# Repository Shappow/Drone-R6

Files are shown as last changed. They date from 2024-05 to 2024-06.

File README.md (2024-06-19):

# BravaBot - General README
#### ⚠️ This project is a work in progress, not all features works and there are bugs ⚠️
The BravaBot is a project meant to make a remote controlled ground vehicule capable of shooting projectiles with a barrel. <br>
In this repository, you will have 4 major folders which describes every important part of the robot. They all have a README into it and that you must follow for to build the vehicule correctly. 
- Electrical Schematics and components you need
- 3D files 
- Android application made on Unity to pilot the vehicule
- Raspberry Pi files to setup and make the vehicule work <br>
The building instruction are into the "datasheet.pdf" file.

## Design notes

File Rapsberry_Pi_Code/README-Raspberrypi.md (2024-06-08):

# Rapsberry-Pi configuration
#### ⚠️Before making any of the following instructions, be sure to setup all of the electronics. You also need a SD card that has at least 16GB of space⚠️

Welcome to the configuration of the raspberry pi. This file will be seperated between to 3 major parts : 
1. Raspberry Pi Setup
2. Camera, Network and video-streaming
3. Motors and canon configuration

Be sure to make to follow in order the steps.

## 1. Raspberry Pi setup 
For this step you will need : 
- A RaspberryPi 3b+ 
- A microSD card which has at least 16GB of storage 
- A SD card/micro SD card reader for you computer/laptop if they  do not have one
- A monitor to connect to the raspberry pi via its HDMI port
- A mouse and keyboard to connect to the USB ports of the raspberry pi

#### ⚠️You will flash a new OS on your MicroSD card. Everything will be erased on it. Be sure to backup everything before making any further step. ⚠️

You can follow this tutorial to setup your raspberry pi 
https://www.youtube.com/watch?v=g2e9RTcXKwg <br>
However you must be aware of the differences :
- The device must be a raspberry pi 3B+
- You need to get the lastest OS version
- You only need to setup the Wifi in "edit settings" you can adapt your country if you want too

After setting up the raspberry pi, open a terminal and install git if not already done (you have to be connected to you wifi) : 
``` bash 
sudo apt-get update
sudo apt-get install -y git
```
And clone in a chosen folder this repository. 
``` bash
git clone https://github.com/Shappow/Drone-R6.git
```
Switch to the Raspberry Pi Branch to save space on your SD card
``` bash
git checkout Raspberry-Pi
```
## 2. Setting up the Network, Camera and Start the video-streaming
### Setting up the camera
For this you will need the **Raspberry-Pi Camera V2**. You can buy it [here](https://www.amazon.fr/Raspberry-Pi-1080p-Module-Caméra/dp/B01ER2SKFS/ref=asc_df_B01ER2SKFS/?tag=googshopfr-21&linkCode=df0&hvadid=194988968614&hvpos=&hvnetw=g&hvrand=10344806919070677782&hvpone=&hvptwo=&hvqmt=&hvdev=c&hvdvcmdl=&hvlocint=&hvlocphy=9055302&hvtargid=pla-195348844379&psc=1&mcid=f413c81c64093678971ae84dd5345588) for example. <br>

Follow this tutorial to setup your camera. You also have a example code to you to check if the camera works.
https://www.youtube.com/watch?v=VzYGDq0D1mw

To be sure that the camera is correctly setup, we will need to be sure that legacy camera option is correctly enabled. <br>
Open a terminal and enter  : 
```bash
sudo raspi-config
```
You should have this interface that opens : <br> 
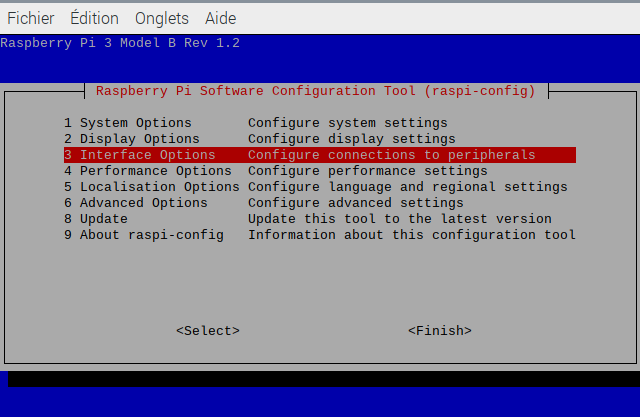
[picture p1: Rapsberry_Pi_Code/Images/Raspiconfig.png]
RaspbeerryPiConfig

Go to Interface Options : <br>
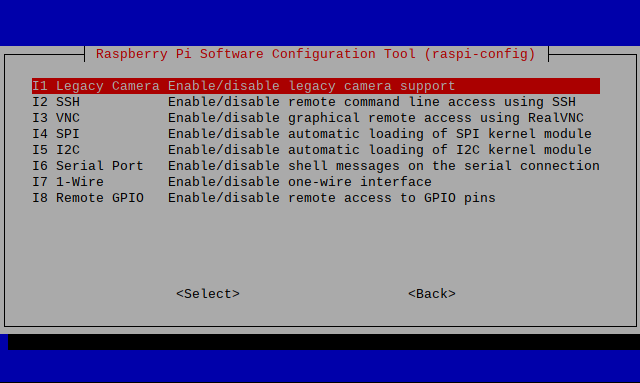
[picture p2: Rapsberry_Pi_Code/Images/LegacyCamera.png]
Interface Options

Go to Legacy Camera : <br>
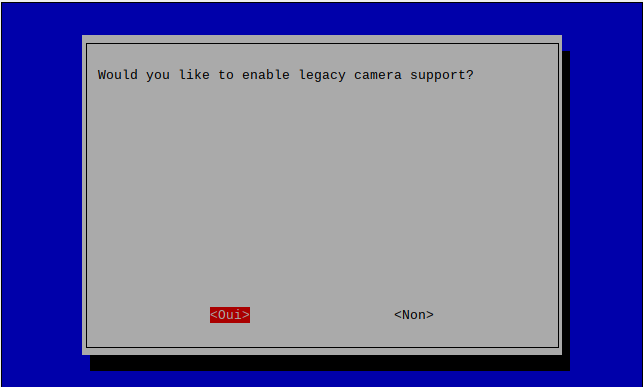
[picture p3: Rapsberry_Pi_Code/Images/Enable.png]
Legacy Camera

And select Yes. After that, use finish and reboot your rapsberry pi. You can do it with this command : 
``` bash
sudo reboot
```
### Importing all of the necessary librairies
Open a terminal in your Raspberry_Pi_Code folder. Be sure the script is executable by doing : 
``` bash
chmod +x imports.sh
``` 
Launch the script to import all of the mandatory libraries.
```
sudo ./imports.sh
```
### Setting up the network
In this step, we will setup the raspberry pi to be a wifi hotspot.
#### ⚠️When the raspberry pi is setup as a wifi hotspot, you can not connect to another wifi. You will be without an internet connection except if you plug in a ethernet cable. You can revert this state and be back to normal by using the "restore_network.sh script.⚠️.
To setup the network, open a terminal in your Raspberry_Pi_Code folder, be sure the script is executable by doing : 
``` bash
chmod +x setup_network.sh
``` 
And start it : 
```
sudo ./setup_network.sh
```
To get back the network to normal, do : 
``` bash
chmod +x restore_network.sh
``` 
```
sudo ./restore_network.sh
```
### Starting the Video streaming server
We will setup the server which will stream the camera feed. Use this command in the Raspberry_Pi_Code folder : 
``` bash
python3 video_stream.py
```
To check if the video stream is working correctly open vlc and go to media>network-streaming, enter http://192.168.4.1:5000 and click on start.
#### ⚠️I am aware that there is a lot of latency. I will work on reducing in the future. The video is stuck at 15 FPS on purpose. You can modify this value in the video_stream.py by changing the value of the variable "FPS"⚠️

## Motors and canon setup

#### This part needs more tests to be fully functionnal + I need to add the coordinates receiver to correctly pilot the robot. For now the code is only made for testing.

Open the main.py, canon.py and motor.py files. Into the main instantiate an object motor and an object canon. Enter the right parameters as asked into the init function. Be aware of the pins it can change depending on the raspberry pi. You can try different funtions to see different behaviors of robot. **Don't forget : the robot will remember the last PWM you put, you could have motors that will still turn even if you stopped the code. Use reset_PWM() in the motors file to stop the pwm.**

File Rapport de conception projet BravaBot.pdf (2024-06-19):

Théo Feugnet – Remy Croizet

# Rapport de conception projet

# Brava Bot

## Sommaire :

## - Introduction - Besoins et objectifs - Choix et justification techniques :

- Outils de gestion
- Composants électroniques
- Outils de programmation
- Choix de design et outils

## - Réalisation :

- Organisation des tâches
- Réalisation de la partie électronique
- Mise en place du schéma électrique
- Réalisation de la partie programmation
- Caméra et réseau sur Raspberry Pi
- Pilotage du BravaBot
- Application mobile
- Réalisation de la partie mécanique
- Conclusion

## Introduction :

## Qu’est-ce que le Brava Bot ?

Le Brava Bot est un drone terrestre commandé par smartphone. Equipé d’une caméra, il permet à l’utilisateur d’avoir une vision sur les mouvements du Brava Bot même s’il est éloigné. Il possède une tourelle pilotable capable de tirer des projectiles grâce à un électro-aimant. Son système de roues mécanum lui permet de réaliser des mouvements précis dans un plan 2D.

## Quelle a été notre inspiration ?

Le Brava Bot est inspiré du drone de l’opérateur Brava (https://rainbowsix.fandom.com/wiki/Brava) dans le jeu vidéo Rainbow Six Siege. Le design est proche, cependant, la fonction de notre Brava bot est différente de par sa capacité à tirer des projectiles.
Voici un exemple de design dont nous nous sommes inspirés :

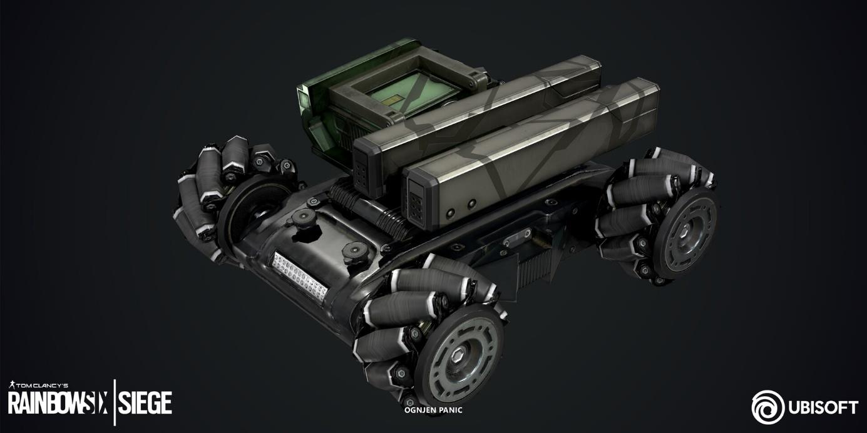
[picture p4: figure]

Pour plus de vues différentes, vous pouvez cliquer ici. (https://www.artstation.com/artwork/n0QWdr)

## Pourquoi réaliser ce projet ?

Ce projet a été réalisé en tant que projet de fin d’année. Nous l’avons choisi car nous aimons beaucoup le jeu d'où provient le drone. De plus, les défis techniques apportés par ce projet nous allaient nous apporter beaucoup de nouvelles compétences et connaissances.

## Comment a-t-on séparé le travail ?

Durant ce projet, nous avons séparé le travail de cette façon :
- Théo s’est occupé de la partie programmation et électronique
- Rémy s’est occupé de la partie design 3D et mécanique

## Objectifs et besoins :

Pour réaliser ce projet, nous avons défini des besoins. Voici ces besoins et leur solution :

Besoin : Pouvoir se déplacer précisément dans un espace confiné.
Solution : le déplacement omnidirectionnel capable de se déplacer librement sur un plan en 2D

Besoin : Pouvoir suivre les mouvements du robot sans avoir une vision directe sur lui Solution : Une caméra embarquée qui permet de suivre les mouvements du robot.

Besoin : Pouvoir commander le robot à distance
Solution : Une application mobile capable de contrôler le robot tant qu’il est connecté à un réseau wifi

Besoin : Être capable de viser avec le canon
Solution : Une tourelle contrôlée par 2 servomoteurs qui lui permette un mouvement rotatif horizontal et vertical

## Choix et justification techniques :

## Outils de gestion :

Présentation Organisation :

Avant de réaliser le projet, nous avons d’abord dû nous organiser. Pour cela nous avons envisagés 2 façons différentes :
- La méthode du cycle en V, basée sur un planning fixe avec des étapes prédéfinies dans le temps, une analyse très poussée des besoins du client et des risques. Elle est pensée avec des objectifs à long terme mais limite parfois la flexibilité d’un projet en cas de problème d’organisation et de définition des besoins du client. La communication se fait principalement par l’intermédiaire de documentation préalablement définie au début du projet.
- La méthode agile, basée sur un planning flexible, découpe le projet en de multiples tâches à court objectifs. Grâce à ce système, nous pouvons créer le projet petit à petit et adapter selon les retours du client et l’avancement du projet. Ce système requiert beaucoup de communication entre les différentes personnes qui travaillent sur le projet ainsi qu’avec le client. Une mauvaise répartition des tâches peut ralentir considérablement le projet et une mauvaise communication peut perturber fortement la qualité du projet. Pour chacun de ces outils nous aurions pu utiliser différents outils :
Pour le Cycle en V, on utilise en général des diagrammes de Gantt. Ils sont basés sur un planning précis avec des tâches à réaliser dans un ordre précis et dans une certaine période.

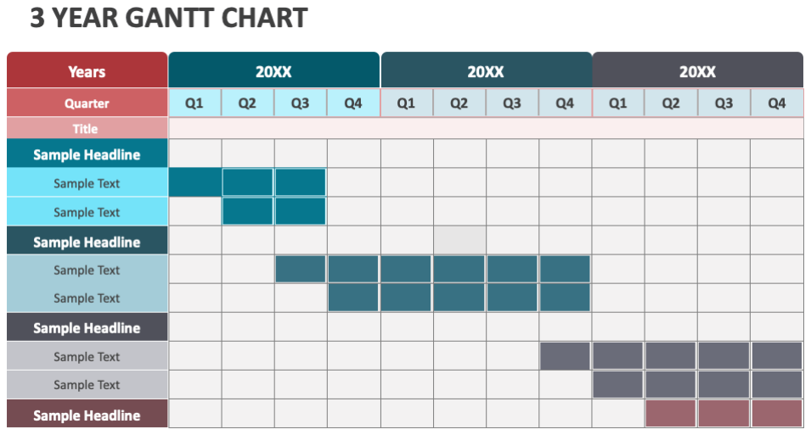
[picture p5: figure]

Voici quelques logiciels/compagnies qui proposent des diagrammes gantt :

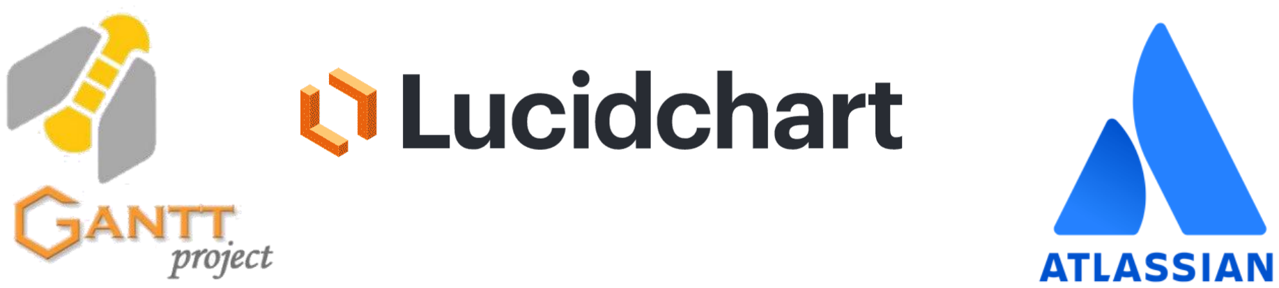
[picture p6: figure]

Pour les méthodes agiles, on utilise en général plusieurs outils, notamment les tableaux kanban, du versionning de projets et des moyens de communication directs. Ils permettent d’organiser son travail en tâches qui avancent au fur et à mesure du projet.

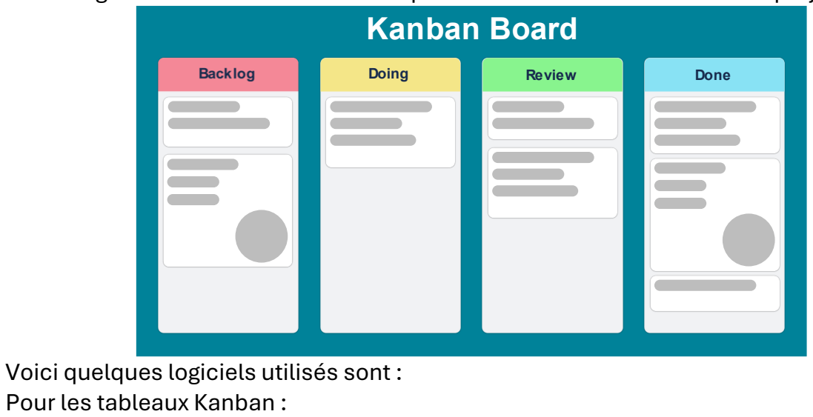
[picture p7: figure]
Pour les tableaux Kanban :

Voici quelques logiciels utilisés sont :

Pour le versionning :

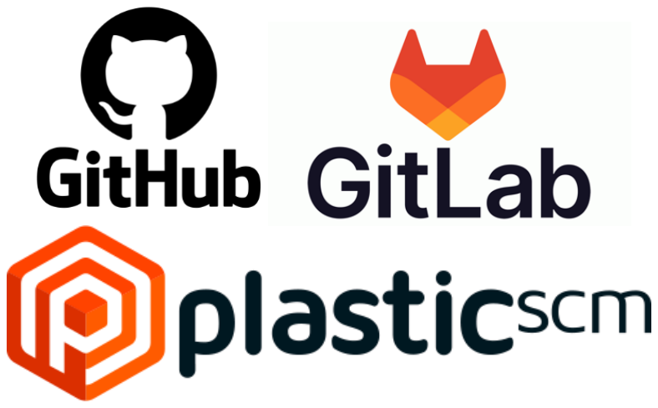
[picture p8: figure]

Les moyens de communication :

Nos choix :

Lors de notre projet, nous avons finalement choisi de nous inspirer de la méthode agile. Il y a plusieurs raisons à cela :
- La flexibilité : en faisant le point sur nos compétences, nous avons conclu que nous étions dans une phase d’apprentissage. Pour définir un Gantt nous aurions eu besoin de beaucoup de notions dans le domaine pour mettre en place chaque étape dans le temps et tenir les délais. Nous avons donc choisi la méthode agile, plus flexible, pour adapter notre travail du lendemain en fonction du travail réalisé le jour-même et les jours précédents.
- La temporalité : notre projet se réalisait sur une période temps relativement courte (11 jours de 8h en cours + 12 jours en travail d’autonomie sur la partie programmation). Mettre en place un planning sur cette période courte n’était pas nécessaire.
- Beaucoup d’évènements bloquants : durant notre projet, beaucoup de facteurs pouvaient nous ralentir. On y retrouve notamment : le temps d’impression 3D, les problèmes avec le matériel que nous avons choisi et de la programmation qui prend plus de temps que prévu.

Pour organiser notre travail, nous avons choisi 3 logiciels :
Pour le tableau kanban nous avons choisi Trello. Il y a plusieurs raisons à le choisir par rapport à Jira.
Jira est un des tableaux kanban les plus complet et utilisé du marché, il est très polyvalent et complet (issue tracking, modularité, création d’user stories). Il demande cependant beaucoup de travail en amont pour pouvoir le mettre en place.
Trello quant à lui est un tableau kanban simple parfait pour des petits projets en équipe réduite qui ne demandent pas beaucoup organisation. De plus, contrairement à Jira, Trello est gratuit.
Etant en binôme, dans un petit projet et très limité dans le temps, nous avons décidé de choisir la solution simple et gratuite pour accélérer le projet.

Pour les outils de versionning, nous avons choisi GitHub.
Il existe de nombreux outils de versionning, mais dans notre situation, plusieurs critères nous ont amenés à choisir cette plateforme.
- Sa popularité. Reconnue dans le monde entier, GitHub est la plateforme la plus utilisé. Elle pourra plus tard nous servir dans nos vies professionnelles à exposer nos projets.
- Son prix. Elle est gratuite !
Pour la communication, nous avons choisi Discord.
Le choix est plus personnel. Nous sommes déjà habitués à l’interface et au fonctionnement de l’application. Nous avons estimé qu’utiliser un logiciel de communication pour le travail ralentirai plus le travail qu’autre chose.
Cependant, dans le cas où nous aurions eu plus de temps, nous aurons pu envisager un logiciel plus adapté au travail comme Slack.

## Composants :

Microcontrôleur / Micro-ordinateur :

Avant de choisir les autres composants, nous avons choisi le composant qui pilote notre robot. Plusieurs microcontrôleurs/micro-ordinateurs se présentent à nous :
Critère | STM32 | Arduino | Raspberry Pi | ESP32
Facilité d'utili-sation | Complexe, né-cessite des connaissances avancées | Très acces-sible pour les débutants | Relativement facile avec des connaissances en Linux | Moyenne, né-cessite des connaissances en program-mation embar-quée
Performance | Haute pour les tâches en temps réel | Modérée, adaptée aux projets simples | Très haute, ca-pable de multi-tâche et de traitement in-tensif | Haute, adap-tée aux appli-cations IoT et temps réel
Consomma-tion d'énergie | Faible | Faible à modé-rée | Élevée par rap-port aux micro-contrôleurs | Moyenne, avec modes basse consommation disponibles
Flexibilité de programma-tion | Limitée aux langages de bas niveau (C/C++) | Large biblio-thèque, IDE simplifié | Supporte de nombreux lan-gages et outils | Supporte FreeRTOS, Ar-duino IDE, et PlatformIO
Coût | Modéré à élevé selon les mo-dèles | Généralement faible | Modéré à élevé selon les mo-dèles | Modéré, mais parfois plus coûteux que les Arduino de base
Connectivité et périphériques | Diverses inter-faces intégrées | Extensible avec des Shields | Intégration éle-vée (Wi-Fi, Bluetooth, USB, etc.) | Wi-Fi et Blue-tooth intégrés, diverses inter-faces
Applications idéales | Industrielles, médicales, temps réel | Éducation, prototypes ra-pides, IoT simples | Serveurs, do-motique avan-cée, médias, projets com-plexes | IoT, applica-tions connec-tées, projets nécessitant Wi-Fi et Blue-tooth

Analysons nos besoins. Notre robot doit :
- Être piloté à distance : 2 microcontrôleurs/micro-ordinateurs sont les plus propices : l’esp32 et la Raspberry Pi
- Pouvoir gérer facilement une caméra. L’esp32 et la Raspberry Pi sont tous deux capables de le faire, cependant cela est beaucoup plus facile à mettre en place sur la Raspberry Pi que sur l’esp32 grâce à son interface graphique
- Être capable de gérer plusieurs programmes en même temps, par exemple un serveur web capable de streamer en direct le retour caméra du robot, recevoir les instructions de déplacement et faire bouger les moteurs en conséquence tout en mettant en place un réseau wifi. Cela demande beaucoup de ressources en même temps, il est donc plus intéressant d’utiliser la Raspberry pi.
Nous pouvons donc en conclure que la Raspberry pi est notre meilleur choix, cependant cela vient aussi avec des désavantages, notamment au niveau de sa consommation électrique qui réduit la durée de fonctionnement du robot. Le projet pourrait probablement aussi se réaliser sur une esp32, mais il serait beaucoup plus dur à mettre en place et il pourrait rencontrer des problèmes de puissance de calcul.
Roues :

Avant de choisir les moteurs, nous devons d’abord choisir quelles roues prendre. Nous avons sélectionné 2 types de roues.
Les roues classique :
Avantages | Inconvénients
Simplicité de conception | Mobilité limitée (uniquement en avant, en arrière, et en tournant)
Robustesse et durabilité | Manœuvres de rotation moins précises sur place
Efficacité énergétique | Difficulté à naviguer dans des espaces restreints ou encombrés
Moins coûteuses | Moins de flexibilité en termes de mouve-ment
Facilité de maintenance | Nécessite plus d'espace pour tourner ou manœuvrer

Les roues Mecanum :
Avantages | Inconvénients
Mobilité omnidirectionnelle | Conception et fabrication plus com-plexes
Capacité à se déplacer latéralement, diagonalement, et à tourner sur place | Coût plus élevé que les roues normales
Grande flexibilité de mouvement | Consommation d'énergie plus élevée
Meilleure manœuvrabilité dans des es-paces restreints | Nécessite un contrôle et une program-mation plus sophistiqués
Permet des mouvements fluides et pré-cis | Peut nécessiter plus d'entretien en raison de la complexité mécanique

Pour notre robot, nous avons décidé d’avoir un déplacement précis même dans des espaces restreints. Cela nous a poussé à choisir 4 roues mécanum FIT0654. De plus, le choix de notre micro-ordinateur, la Raspberry pi, peut simplifier la mise en place de l’algorithme gérant le mouvement des roues mécanum. Cependant, les roues mecanum sont un mauvais choix dans la situation le terrain difficile. Une alternative serait les chenilles omnidirectionnelles, mais ces chenilles sont très couteuses, très complexe à mettre en place mécaniquement et encore en développement (Source : MDPI Applied Sciences). (https://mdpi-res.com/d_attachment/applsci/applsci-11-11778/article_deploy/applsci-11-11778-v2.pdf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)
Moteurs :

Pour les moteurs, nous sommes allés au plus simple : 4 moteurs à courant continu avec réducteurs simples. (Moteur à courant continu DC3V-12V). Cela était principalement un choix budgétaire et de complexité. Cependant, après la réalisation du projet et des recherches approfondies, des moteurs brushless auraient pu être un meilleur choix : leur couple est élevé et constant et ils nécessitent moins d’entretien. Cependant cela aurait demandé de mettre en place des ESC (electronic speed controls) supplémentaires pour fonctionner correctement. Il est aussi beaucoup plus complexe à utiliser qu’un simple moteur à courant continu.

Servo Moteurs :

Pour bouger le canon, nous avons besoin d’une grande précision. L’idéal est de pouvoir directement choisir un angle et diriger ainsi le canon. Pour cela nous avons choisi le servo moteur sg90. La raison principale est son prix très faible et sa facilité d’utilisation. Mais il limite l’angle et le couple. D’autres servos moteurs peuvent être intéressants pour ce projet, comme le mg90s avec ses engrenages en métal qui assure une plus grande durabilité et un couple plus élevé pour un prix presque semblable ou encore le FS90R avec sa rotation continue qui aurait été idéale pour faire tourner le canon à 360 degrés facilement.

Pont en H :

Pour ce projet, nous avons utilisé 2 ponts en H L298N. Ce sont de bons ponts en H apportant une bonne dissipation thermique avec une tension de fonctionnement très large (5V à 35V) avec un courant de sortie par canal de 2A. Une autre alternative similaire aurait été possible comme le DRV8833 qui a une meilleure efficacité énergétique mais qui limite la tension de fonctionnement de 2,7V à 10,8V et 1,5A par canal.

Batterie :

Pour ce projet, nous avons dû choisir une batterie qui devait respecter la petite taille de notre robot, tout en lui proposant une tension et un courant suffisant en lui assurant une bonne autonomie. Lorsque l’on réalise le bilan énergétique, nous avons ce résultat.
Critère | SG90 | Raspberry Pi 3B+ | L298N | Moteurs DC
Courant | 100-250 mA 360mA en stall | 800mA maxi-mum | Courant lo-gique : 0-36mA | 160 mA - 220 mA 250 mA max
Tension | 4.8-6V | 5V | 5V-35V pour l’alimentation des drivers 5V alimenta-tion logique | 3V - 12V
Puissance | 2,16W | 4W | 0,18W pour le courant lo-gique 140W pour le courant des drivers combi-nés | 1,8W

Total maximum : 0.036*2+0.8+0.36*2+0.25*4 : 2,592A
Nous avons à l’origine opté pour une batterie 11,1 V 5000 mAh cependant, sa taille et son poids étaient trop conséquents. De plus, une tension si élevée n’était pas nécessaire au bon fonctionnement du robot, bien que les moteurs puissent supporter un max de 12V. Nous avons donc opté pour une batterie de 7,4V à 6800mAh pour une taille plus petite et un poids plus faible en assurant en plus une durée de vie plus longue.

Logiciel pour schéma électronique :

Ce logiciel a permis de créer un schéma électrique adapté aux composants présents dans le projet. Il a été choisi pour sa simplicité et sa gratuité (relative car uniquement présente sur les versions bêta du logiciel).

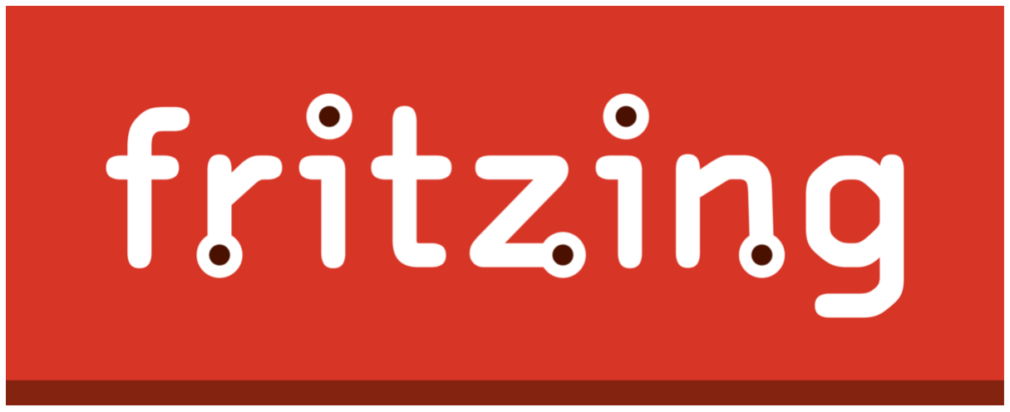
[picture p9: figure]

## Outils de programmation :

Programmation sur la Raspberry Pi

Pour programmer sur la Raspberry Pi, nous avons utilisé 2 IDE et le terminal linux, tous deux natifs sur le micro-ordinateur.
- Thonny IDE, adapté à la programmation sur microcontrôleur, il simplifie la communication entre le code et le microcontrôleur, permettant de téléverser du code MicroPython sans passer par des plugins supplémentaires comme sur Visual Studio Code. Cependant programmer est moins confortable que sur un IDE plus moderne comme Visual Studio Code dû au manque d’extensions que l’on peut lui ajouter.
- Geany, un IDE polyvalent natif à l’OS de Raspberry pi. Il supporte notamment le C, C++, Python, Java, PHP, HTML, JavaScript, et Perl mais il supporte aussi d’autre langages comme le Shell. Cependant, il n’est pas très avancé, et Visual Studio Code aurait probablement été un meilleur choix que cet IDE.
- Le terminal linux intégré à l’OS Raspberry Pi. Obligatoire pour le bon fonctionnement du projet, il est natif et non remplaçable.

Programmation de l’application Android

Pour programmer l’application Android, il était obligatoire de choisir un IDE/moteur de jeu capable de réaliser ce que l’on souhaitait.
2 choix s’étaient présentés à nous :

Android Studio propose une meilleure optimisation pour l’application, et indirectement, moins de consommation électrique. Cependant il ne fonctionne que sous Android et serait incompatible avec les produits Apple par exemple. Il limiterait aussi des options graphiques.
Unity quant à lui est plus lourd et complexe, mais il permet d’exporter l’application sur d’autres plateformes. Il permettrait aussi de réaliser d’autres fonctionnalités en 3D comme la trajectoire du tir.

## Choix de design et outils :

Croquis et idéation

Nous avons débuté le processus de conception par la réalisation de croquis à main levée sur papier. Cela nous a permis de formaliser nos idées initiales, d'affiner le design final, de définir les dimensions et les capacités de l'objet. Cette étape préliminaire s'est avérée cruciale pour visualiser l'ensemble du projet et anticiper les potentielles contraintes techniques.

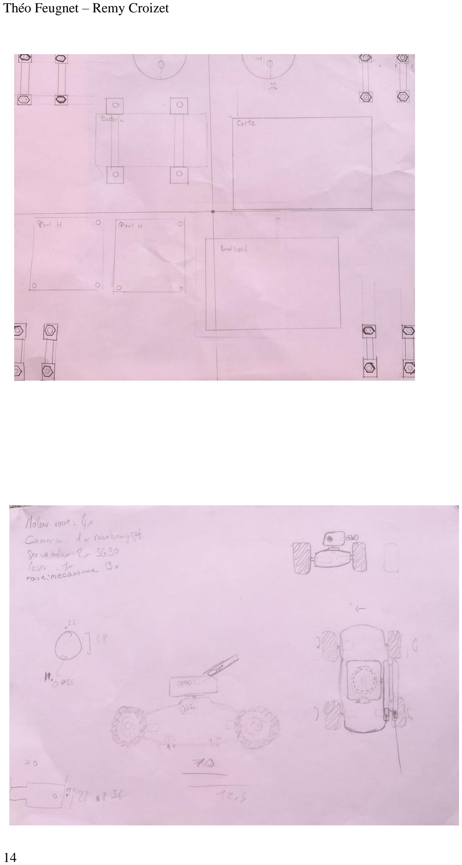
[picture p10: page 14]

Design

Nous avons donc décidé de faire une fusion entre le design du robot avec lequel on s’est inspiré tout en y mettant notre petite touche personnelle. Ainsi, nous avons choisi de le combiner à un char d'assaut, pour nous rapprocher d’une de nos passion commune, les jeux vidéo.

Choix du logiciel de CAO

Une fois les croquis finalisés, nous avons franchi le pas vers la conception numérique. Plusieurs logiciels de CAO (Conception Assistée par Ordinateur) s'offraient à nous, chacun avec ses propres forces et faiblesses. Parmi les options les plus populaires figuraient Solidworks, Fusion 360, Autodesk Inventor, CATIA, Siemens NX, PTC Creo Parametric et pleins d’autre choix divers et variés.

Sélection de Fusion 360

Après une analyse approfondie des différents logiciels, j'ai porté mon choix sur Fusion
360. Cette décision s'est basée sur plusieurs facteurs :
- Maîtrise du logiciel : Je possède déjà une certaine expérience dans l'utilisation de Fusion 360, ce qui me permet de travailler de manière efficace et efficiente.
- Facilité d'utilisation : Fusion 360 est réputé pour son interface intuitive et sa prise en main relativement aisée,même pour les utilisateurs débutants.
- Fonctionnalités complètes : Le logiciel offre un éventail complet d'outils de modélisation, de simulation et de fabrication, répondant ainsi parfaitement aux exigences de mon projet.
- Flexibilité : Fusion 360 s'adapte à une large variété de domaines d'application, de la conception mécanique à la fabrication de prototypes.
- Travail collaboratif : Fusion 360 est un logiciel de CAO proposant un système de cloud partagé qui permet donc de travailler facilement et efficacement à plusieurs sur un même projet. De plus, il est aussi accessible depuis un navigateur internet, sans installer l’application sur son pc, cependant cela nécessite une très bonne connexion.

En conclusion, le choix de Fusion 360 s'est révélé judicieux et m'a permis de mener à bien la phase de conception 3D du projet de manière efficace. Le logiciel s'est imposé comme un outil indispensable, tant pour la modélisation que la fabrication. Ses fonctionnalités de partage nous on permit d’accéder facilement aux pièces à n’importe quel moment sans avoir à demander de l’aide aux autres collaborateurs pour y accéder.

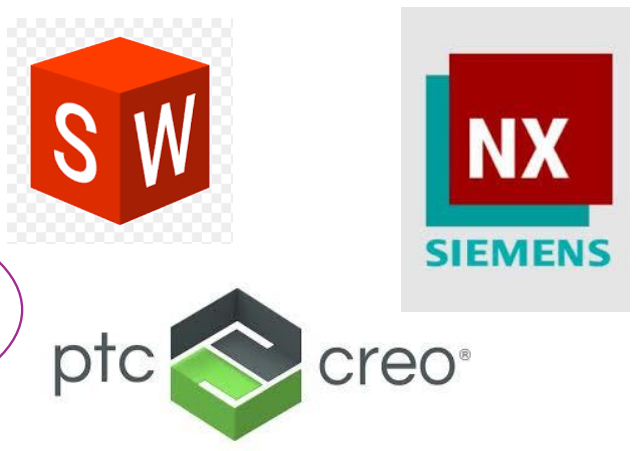
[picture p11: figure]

## Réalisation :

## Organisation des tâches :

Pendant les 3 premières séances (2 avril, 15 avril, 16 avril), nous avons organisé le projet.
Nous avons d’abord décidé dans quel projet faire. Nous avons défini les fonctionnalités que nous allons réaliser dans ce projet. Ce sont les suivantes :
- Avoir un déplacement omnidirectionnel
- Pouvoir se piloter à distance grâce à un réseau Wifi sur une application Android
- Recevoir un flux vidéo constant sur l’application grâce à une caméra embarquée sur le Brava Bot
- Avoir une tourelle rotative capable de tirer un projectile en métal
Nous avons séparé le projet en tâches dans un tableau kanban à la façon de méthodes agile, pour pouvoir avancer à notre rythme en prenant compte des imprévus.

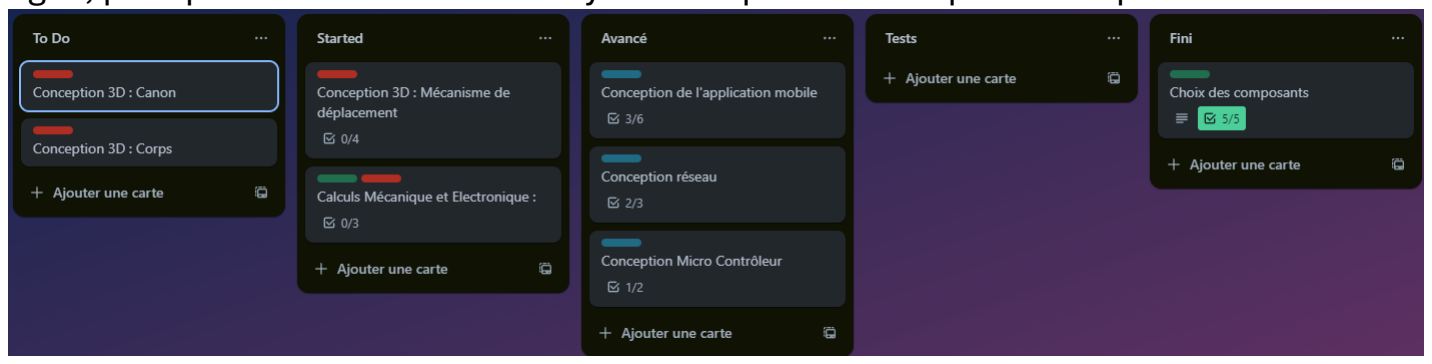
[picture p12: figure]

Dans chaque carte se trouve une petite étape de la tâche :

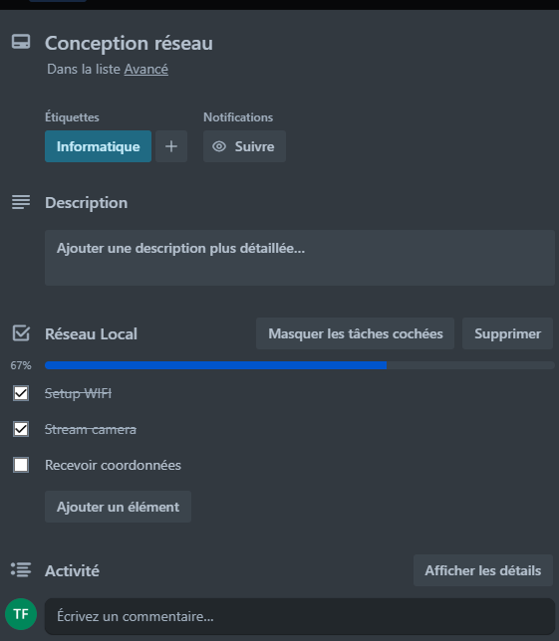
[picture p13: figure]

Théo s’est occupé de la partie programmation et électronique.
Rémy quant à lui s’est occupé de la partie design 3D et mécanique.
Durant tout le projet, nous avons beaucoup communiqué, chaque jour le matin pour savoir ce que l’on allait faire dans la journée et parfois, quand nécessaire discuter sur des modifications à réaliser dans la conception de base du robot.
Le 22 avril nous avons réalisé une présentation du MVP. Nous avons pu présenter les différentes fonctionnalités qui devraient être présentes sur la version minimale du projet.
Le 14 mai nous présentions le MVP dans son état.
Le 9 juin nous rendons ce document ainsi que le dépôt git.

## Réalisation de la partie électronique :

Après la mise en place du projet les 2 premiers jours ont été consacrés à la mise en place de la recherche de composants. Se référer à la partie « Choix des composants pour plus d’informations ».
Durant tout le projet, le schéma électrique a dû être mis à jour. Le voici :

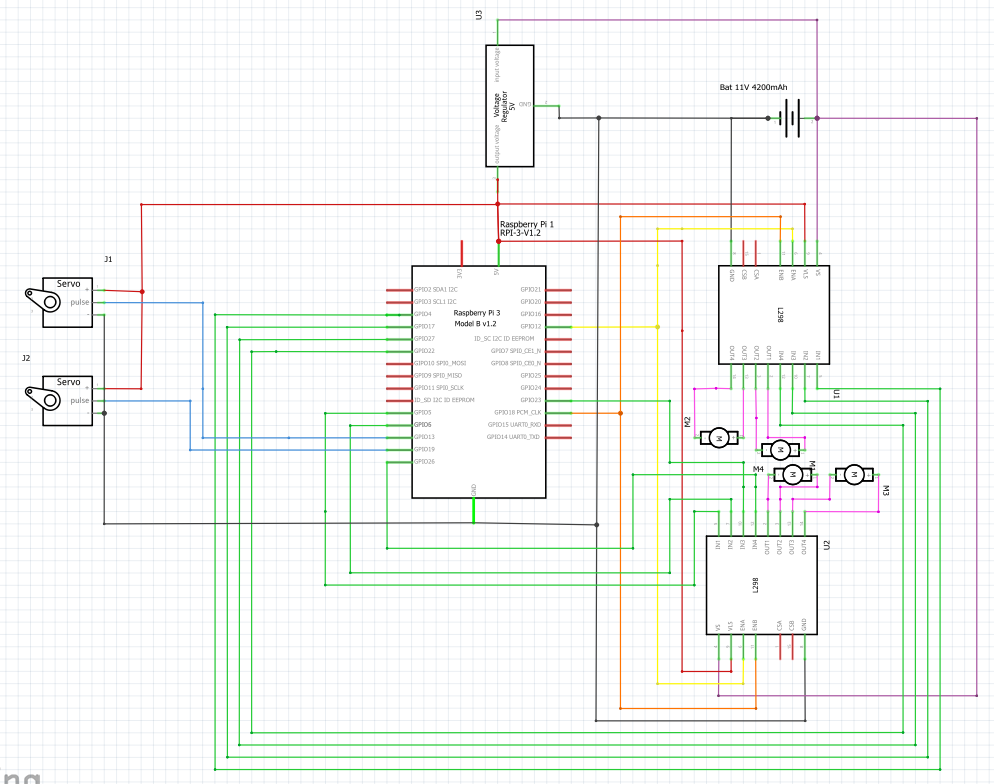
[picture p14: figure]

Cette partie correspond aux 4 moteurs et à leur pont en H L298N qui pilotent le robot. Ils servent à faire bouger les roues mécanum dans le bon sens et à la bonne vitesse.

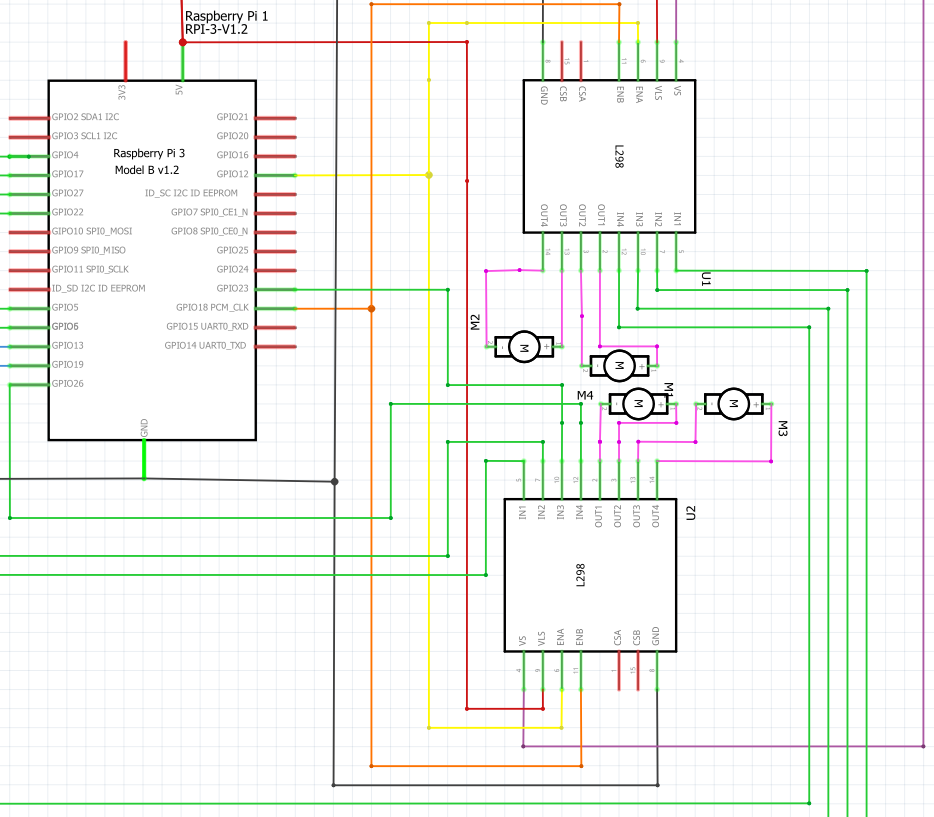
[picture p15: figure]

Chaque câble vert correspond à un pin « in » . Ils ont chacun leur propre pin afin d’assurer le sens de rotation individuel de chaque moteur. Ils peuvent avoir un état haut ou un état bas.
Les câbles orange sont les pins enB PWM des deux L298N. Ils sont tous les deux reliés pour partager la même vitesse.
Les câbles jaunes sont les pins enA PWM des deux L298N. Ils sont tous les deux reliés pour partager la même vitesse.
Les câbles noirs correspondent à la masse.
Les câbles rouges connectent le régulateur de tension à l’alimentation logique en 5V. Les câbles violets connectent la batterie à l’alimentation des moteurs en 7.2V.
Les câbles roses sont les câbles reliés aux canaux du L298N. Selon le pin in qui est activé le code le L298N va alimenter l’un des câbles faisant tourner le moteur dans un sens où dans l’autre. Si les deux in sont à l’état haut ou à l’état bas, le L298N n’alimente aucun des fils.

Voici un schéma qui explique comment les pins moteurs sont séparés.
Front

+--+------------+--+
| \ |F1 F2| / |
|\ |enA enB| / |
+--+ | +--+
+--+ | +--+
| / |enB enA| \ |
| / |B1 B2| \ |
+--+-------------+--+
Back

Cette partie est réservée aux servo-moteur :

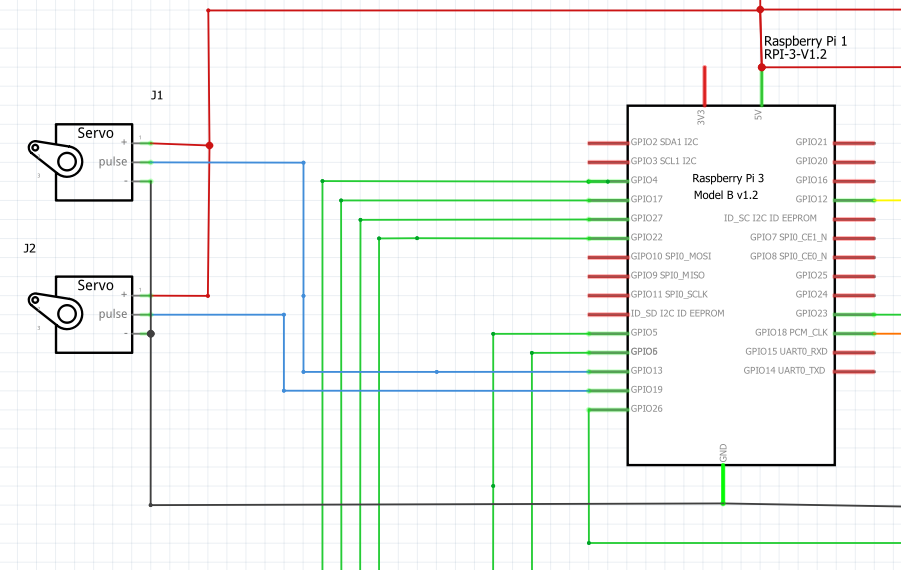
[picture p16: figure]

Le câble bleu est relié à un pin PWM. Selon le signal PWM que l’on lui transmet, il va bouger à un certain angle.
Les câbles rouges alimentent le servo moteur depuis le régulateur de tension.
Les câbles noirs sont reliés à la masse.
Les servos moteurs servent à diriger le canon à 180° horizontalement et à 180° verticalement.

Cette partie est réservée à la batterie :

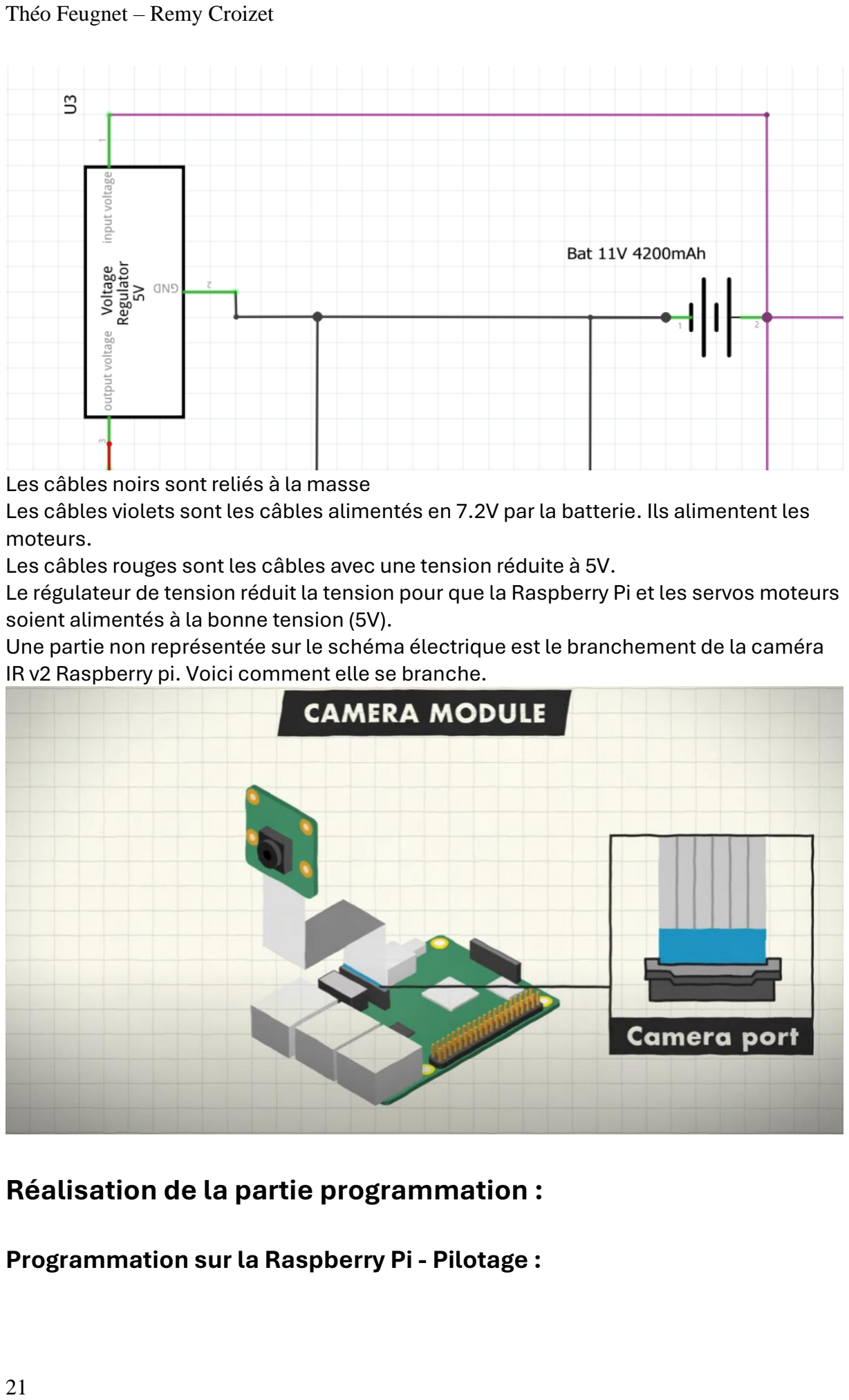
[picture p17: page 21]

Les câbles noirs sont reliés à la masse
Les câbles violets sont les câbles alimentés en 7.2V par la batterie. Ils alimentent les moteurs.
Les câbles rouges sont les câbles avec une tension réduite à 5V.
Le régulateur de tension réduit la tension pour que la Raspberry Pi et les servos moteurs soient alimentés à la bonne tension (5V).
Une partie non représentée sur le schéma électrique est le branchement de la caméra IR v2 Raspberry pi. Voici comment elle se branche.

## Réalisation de la partie programmation :

Programmation sur la Raspberry Pi - Pilotage :

Cette partie a été majoritairement réalisée pendant la période de cours de notre projet. Elle a été travaillée du 22 avril au 13 mai les mardi et lundi.
Dans cette partie, l’objectif était de réaliser un algorithme capable de contrôler les mouvements du robot en fonction des informations renvoyées par le joystick sur l’application.
On utilise un système de « case ». Selon la position du joystick, on va donner comme ordre au robot de faire un certain mouvement en particulier. Plus le joystick s’approche d’un des bords, plus la vitesse augmente, plus il se rapproche du centre, plus elle réduit. Au centre se trouve une « deadzone » où le robot ne se déplace pas.
Le joystick droit s’occupe de la translation :

Le joystick gauche s’occupe de la rotation :

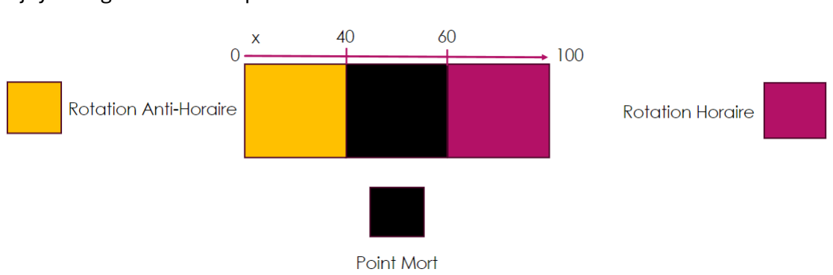
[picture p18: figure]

Pour réaliser ces mouvements, il faut réaliser des mouvements de bases pour les roues mécanum :

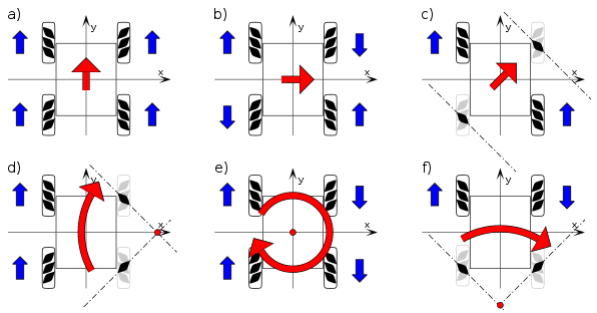
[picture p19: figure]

Comme décrit dans le schéma ci-dessus, le sens de rotation des roues ou le fait qu’elles soient à l’arrêt fait varier les mouvements.
Dû au choix des ponts en H L298N, nous devons fonctionner avec 12 pins, 3 par moteur :
- Le pin en (A ou B selon le canal). Il reçoit un signal PWM qui fait varier la tension du moteur pour changer sa vitesse.
- Le pin in1 (pour le canal A) ou in3 (pour le canal B), qui reçoit un signal binaire. Selon son état il peut faire tourner le moteur dans le sens horaire.
- Le pin in2 (pour le canal A) ou in3 (pour le canal B), qui reçoit un signal binaire. Selon son état il peut faire tourner le moteur dans le sens anti-horaire.
Chaque LN298 possède 2 moteurs attaché.
Cependant, comme précisé dans le schéma plus haut dans la partie électronique les PWM des moteurs sont reliés en croix. Les pin PWM sur la Raspberry pi sont limités. Utiliser ce système permettra d’ajouter les servos moteurs en plus. Malgré la réduction du nombre de pins PWM, cela n’impacte pas les mouvements possibles par le robot.
En respectant le sens des pins In selon les coordonnées, nous pouvons définir le mouvement que le robot va réaliser. Selon la position dans la zone où il se trouve, on peut faire varier sa vitesse.
Le code se sépare en 2 fichiers :
Un fichier moteur.py composé d’une classe qui contient toutes les méthodes nécessaires pour initialiser les moteurs et les piloter selon des coordonnées.

Elle contient 5 méthodes :
- La méthode __init__ qui instancie la classe. Ses paramètres sont les pins EnA, EnB, les pins in1, in2, in3, in4 des moteurs à l’avant et à l’arrière.
- La méthode reset_PWM qui arrête tous les moteurs.
- La méthode moveMotor qui fait bouger un moteur précis selon une vitesse et un sens de rotation. Il prend en paramètre le côté du moteur (avant ou arrière), le nom du moteur, son sens de rotation et sa vitesse.

- La méthode rotation qui prend en paramètre des coordonnées X et décide du sens et de la vitesse de rotation du robot. Elle utilise moveMotor pour bouger les moteurs.
- La méthode translation qui prend en paramètre des coordonnées X Y et décide du mouvement à effectuer et de sa vitesse. Elle utilise moveMotor pour bouger les moteurs.
Un fichier main.py qui instancie la classe Moteur, s’occupe de recevoir les coordonnées et les envoie aux méthodes de l’objet Moteur pour réaliser des mouvements sur le robot.
Programmation sur la Raspberry Pi – Réseau wifi, serveur de streaming et Caméra :

Cette partie a été réalisée après la fin des cours en présentiel, donc en pure autonomie. L’objectif est d’utiliser la Raspberry Pi comme un relais wifi dont on se connectera avec son smartphone. En se connectant à une adresse IP précise, nous pouvons recevoir le flux vidéo de la caméra.
La mise en place du réseau wifi est importante pour notre projet car elle va nous permettre de communiquer facilement avec le robot à distance. Pour le mettre en place, nous allons utiliser les daemons dhcpcd, hostadp et dnsmasq. En modifiant les fichiers de configuration hostadp.conf, dnsmasq.conf, sysctl.conf, rules.v4 et dhcpcd.conf, nous indiquons à la Raspberry Pi d’émettre un réseau Wifi plutôt que de capter un réseau. Nous créons aussi un fichier de backup dnsmasq.conf.orig au préalable pour sauvegarder l’ancienne configuration. En redémarrant les daemons, nous pourrons alors appliquer les changements.
Lorsque nous mettons en place la Raspberry Pi dans une configuration « point wifi », elle ne peut plus se connecter à d’autres réseaux wifi. Elle est donc déconnectée d’internet sauf si elle utilise un câble Ethernet. Pour cela, nous modifions dhcpcd.conf pour le remettre à la configuration initiale, arrêtons les daemons hostadp et dnsmasq, remplace le fichier dnsmasq.conf par le fichier dnsmasq.conf.orig et redémarre le daemon dhcpcd.
Pour faciliter la mise en place du réseau, nous avons créé des scripts Shell :
- setup_network.sh capable de configurer la Raspberry comme un émetteur Wifi
- restore_network.sh qui remet la Raspberry pi a sa configuration de base
Pour mettre en place un serveur de streaming capable de récupérer de streamer la caméra, nous avons créé le script python video_stream.py.
Il utilise la bibliothèque openCV pour récupérer le flux caméra. Il découpe ensuite le flux vidéo de la caméra en différentes frames et les encode pour qu’elles puissent être envoyé sur le réseau wifi. On utilise ensuite le micro-framework Flask. Il est simple, flexible et léger. Sa modularité lui permet de d’ajouter différents outils pour créer son framework personnalisé avec uniquement les fonctionnalités souhaitées. On ajoute la bibliothèque Gevent pour réduire la latence de la caméra. En effet, son serveur WGSI est plus optimisé que celui de base fournie par Flask.
Programmation de l’application mobile :

Cette partie a été réalisée durant les week-ends les périodes de cours.
Elle utilise Unity pour recevoir le flux vidéo et envoyer des coordonnées sur l’application. Elle possède différents scripts qui permette au code d’envoyer facilement au Raspberry pi les coordonnées des joysticks en permanence et de recevoir le flux vidéo. Voici ce à quoi ressemble l’interface de l’application :

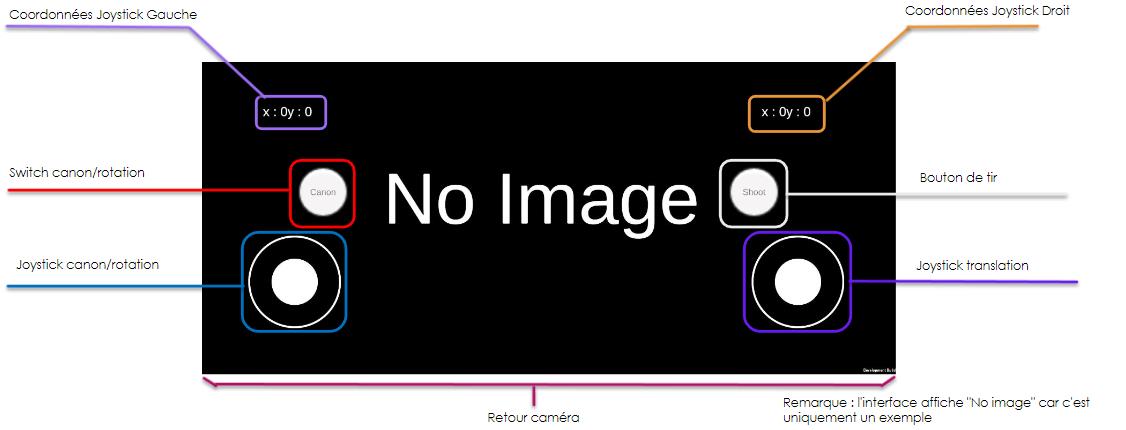
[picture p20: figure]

Le fond d’écran correspond au retour d’image du robot. Il permet à utilisateur de pouvoir de diriger le robot même s’il est hors de vue.
Les coordonnées du joystick gauche (mauve) et les coordonnées du joystick droit (jaune) affichent les coordonnées de leur joystick associé. Elles sont pour le moment temporaires et utilisées pour du débug.
Le bouton (rouge) switch canon/rotation permet à l’utilisateur de modifier l’utilisation du joystick gauche. Ainsi, il peut être utilisé pour faire tourner le robot sur lui-même ou pour faire tourner le canon.
Le bouton (blanc) shoot sert à tirer le projectile présent sur le robot.
Le joystick gauche sert à deux choses : faire tourner le robot sur lui-même ou bouger le canon.
Le joystick droit sert à translater le robot.

## Réalisation de la partie mécanique :

Choix des matériaux utiliser :

Nous avons réalisé une étude des matériaux, Cette démarche nous permet de créer un robot à la fois performant et respectueux des contraintes budgétaires et de durabilité. Chaque choix a été réfléchi pour offrir un résultat optimal afin d’avoir le meilleur rendement qualité/prix possible.

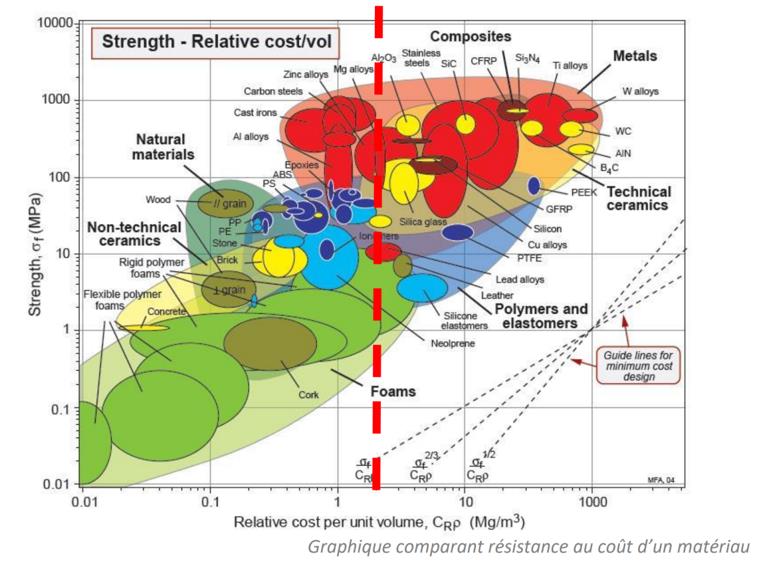
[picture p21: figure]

Sur ce premier graphique nous pouvons comparer le rapport résistance/coût, cette ligne rouge nous sépare à gauche les matériaux entrant dans nos critères et à droite ceux y sortant du au prix relativement élevé.

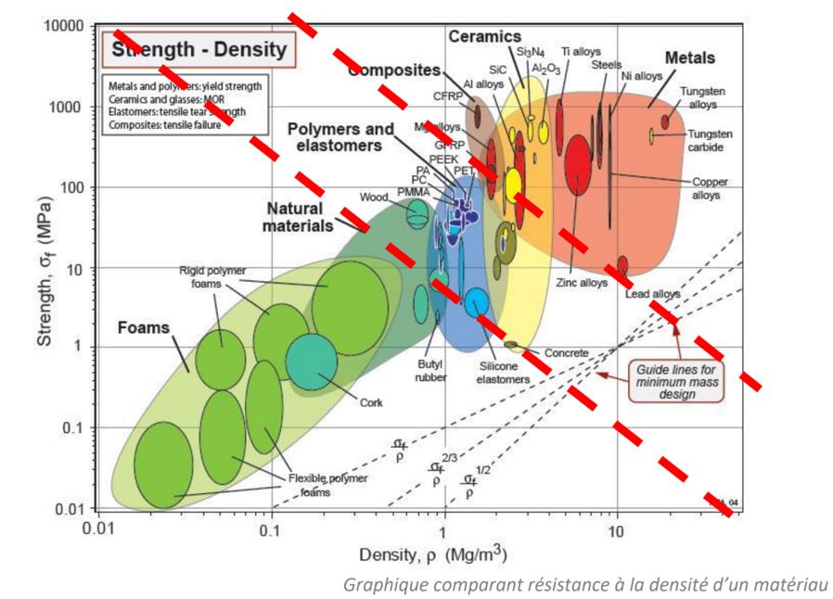
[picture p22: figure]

Entre les deux traits rouges nous pouvons voir les diffèrent matériaux entrent dans les critères de la résistance, nous pouvons constater qu’il ne reste que des polymères et des élastomères, les matériaux naturels tel que le bois n’auraient pas une bonne résistance aux vibrations et pas la stabilité que nous recherchons.

Le métal quant à lui serais trop lourd et nous l’avons déjà enlevé de nos hypothèses sur le premier graphique.

Après s'être rendu compte qu'il fallait que l'on utilise un matériau de
type plastique, nous avons choisi l'impression 3D pour son efficacité et sa précision et fait une étude pour savoir lequel utiliser.

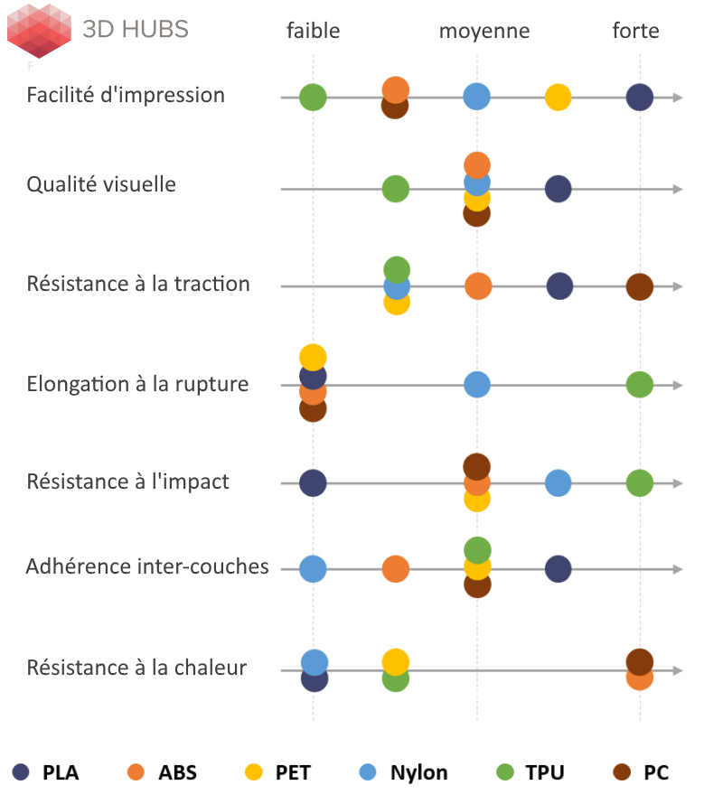
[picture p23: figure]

Nous pouvons donc constater que deux polymères s’ouvrent à nous, le PLA et le PET. Le PLA et PET sont deux types de plastiques couramment utilisés dans l'impression 3D et l'emballage. Bien qu'ils partagent certaines similitudes, ils présentent également des différences importantes en termes de propriétés, d'applications et d'impact environnemental. Le PET n’est pas dégradable ce qi nous touche car nous voulons rester dans un robot qui respect la nature au mieux possible, et le problématique majeur de ce plastique est qu’il est flexible ce qui rend la tâche impossible en vue des pièces que nous avons besoin. Nous avons donc choisi d’utiliser du PLA car c’est le matériel avec le meilleur rapport qualité prix et avec une excellente résistance.
Conception :

Pour la Conception de notre robot, nous aurons besoin d’imprimer quelques pièces :

8 Fixations moteur :

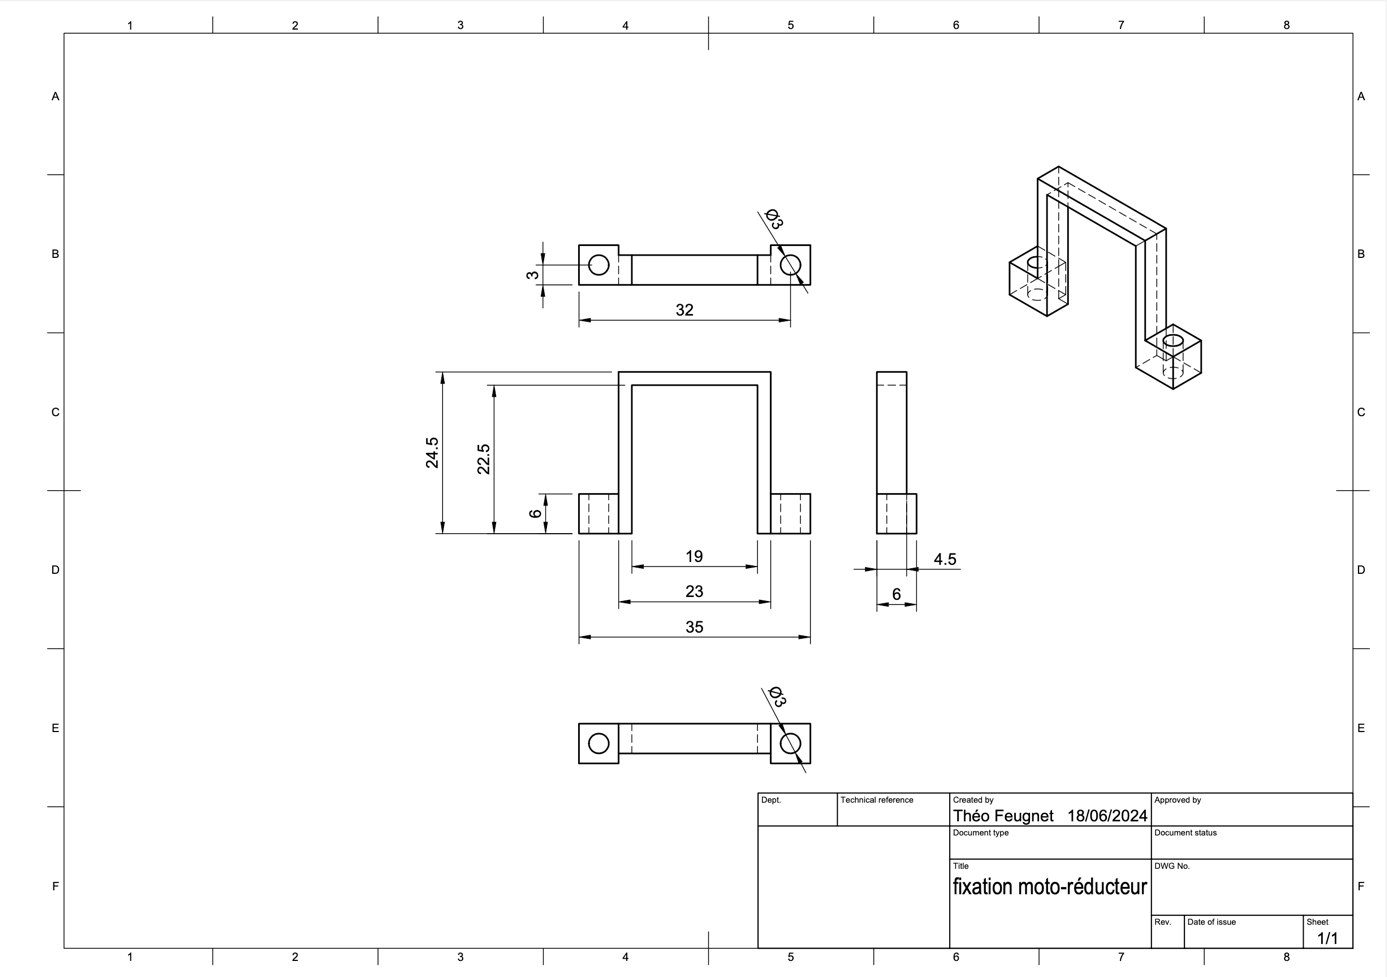
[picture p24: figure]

2 Fixation Batterie :

1 Bases roulante :


1Carter :

1 Tête :


1

Canon :

4 Adapteur d’arbre roue – moteur :

Réalisation :

Le total de notre robot fera une dimension de 200mm sur 250mm avec 250mm de hauteur tout ça pour un poids de 1,3 kg.

Pour ce qui est du montage je vous laisse vous diriger vers la notice de montage.

## Conclusion :

Ce projet nous a permis de beaucoup apprendre. Il nous a mis dans différentes difficultés que nous avons réussi à surmonter dans l’ensemble. Nous sommes fiers de ce que nous avons fait et espérons pouvoir réaliser de nouveau un autre projet semblable.

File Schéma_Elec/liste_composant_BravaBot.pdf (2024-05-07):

## Liste des composants pour le BravaBot :

Logiciel :

- Fusion 360
- Canva
- Word
- Discord
- Trello
- Thonny
- Raspberry pi os
- Fritzing
- GitHub
- Unity 2022.3.4 F1
- Safari
- Opera GX
- Chat GPT
- Google

Fournisseur:

- Ynov campus Bordeaux
- Amazon

Matériel informatique :

- PC portable : x2
- Cable Alimentation correspondant au PC : x2
- Clavier : x1
- Souris :x3
- Écran : x1
- Cable d’alimentation Écran (type F) : x1
- Cable HDMI : x1

Matériel Électroniques :

- Raspberry pi 3 :x1
- Pont en H : L298N : x2
- Abaisseur de tension : LM2596 : x1
- Servo moteur : SG90 : x2
- Moteur à courant continu : DC3V-12V : x4
- Raspberry pi noir camera V2: x1
- Batterie 11.1V / 1500mAh: x1
- Breadboard: x1

Visserie:

- Vis M3x12 : x±35
- Écrous M3 : x±35
- Tournevis : x1
- Embout PH0 : x1
- Clé 6 pan de 3 : x1

Matériel nécessaire à la fabrication :

- Roue FIT0654 : x4
- Générateur Rigol : x1
- Cable d’alimentation Générateur (type F) : x1
- Oscilloscope Rigol : x1
- Cable d’alimentation oscilloscope (type F) : x1
- Sondes oscilloscope :x1
- Multimètre : x1
- Sonde Multimètre : x2
- Imprimante 3D bambu lab x1 carbon : x1
- Imprimante 3D bambu lab P1S : x1
- Cable d’Alimentation imprimante 3D (type F) : x1
- Prise 230v : x5
- Fer à Souder Antex : x1
- Support fer à souder : x1
- Panne de fer à souder : x1
- Éponge fer à souder : x1
- Cable micro USB : x1
- Cable USB C : x1
- Adaptateur pc USB C : x1
- Pied à coulisse : x1
- Réglet : x1
- Crayon à papier : x1
- Gomme : x1
- Lunette : x2

Consommable :

- Cable Dupont
- Rislan
- Bobine PLA
- Bobine éteint

Stockage :

- Carte SD des imprimantes : x2
- Carte SD Raspberry pi : x1
- Boite de rangement : x1
- Stockage interne pc : x1
- Clef USB : x1
- GitHub

Croizet Remy
Feugnet Théo

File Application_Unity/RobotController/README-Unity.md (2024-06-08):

# Unity andoid application
#### ⚠️The application is mostly done but it need more tests⚠️
#### ⚠️Before following this README, please follow the instructions from the raspberry pi README⚠️
## Fast installation :
To install the application, follow these steps :
1. Download the RobotController.apk from Application_Unity/Builds.
2. Plug in your android phone and transfert the application into your storage.
3. Go to your android phone, find the apk and accept the installation.
4. Open the new application and your ready to go

## Opening the project and connecting your phone to Unity
### Installation of the necessary components.
Follow this easy guide to install Unity <br>
https://www.youtube.com/watch?v=DDPd2UKnoaU <br>
Install the 2022.3.32f1 version of Unity and be sure to have these modules : <br>
Module android et Visual Studio 2022
### Opening the project
In the project tab, click on Add.
Button open project
Go and find the "RobotController" folder and select it. Click open.<br>
It will take some time. <br><br>
Meanwhile get your phone and activate the developper mode. Follow this tutorial: https://www.youtube.com/watch?v=gn4bRTFicZw <br>
When the developper mode is activated, turn on the option USB debug in the developper tab. Plug your phone to your PC.<br><br>
Follow these steps when the project is open
Open Build
Select Phone
Build and run
The build will take some time, especially on during the first time.
After that the app will run on your smartphone. You can modify anything you want in the project if you want to modify the project.

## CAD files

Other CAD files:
Fichiers_fusion/Assemblage bravabot.f3z
Fichiers_fusion/Base roulante.f3d
Fichiers_fusion/Canon.f3d
Fichiers_fusion/Carter.f3d
Fichiers_fusion/Fixation batterie.f3d
Fichiers_fusion/Fixation moto-réducteur.f3d
Fichiers_fusion/Moto-réducteur.f3d
Fichiers_fusion/Tête.f3d

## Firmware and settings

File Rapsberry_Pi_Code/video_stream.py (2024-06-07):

from flask import Flask, Response
import cv2
import threading
from gevent.pywsgi import WSGIServer
from gevent import monkey
app = Flask(__name__)
FPS = 15
def generate_frames():
    cap = cv2.VideoCapture(0)
    if not cap.isOpened():
        print("Error: Could not open video device")
        return

    cap.set(cv2.CAP_PROP_FPS, 15)
    cap.set(cv2.CAP_PROP_FRAME_WIDTH, 480)
    cap.set(cv2.CAP_PROP_FRAME_HEIGHT, 210)

    while True:
        success, frame = cap.read()
        if not success:
            print("Error: Could not read frame")
            break
        else:
            ret, buffer = cv2.imencode('.jpg', frame,[int(cv2.IMWRITE_JPEG_QUALITY), 25])
            if not ret:
                print("Error: Could not encode frame")
                break
            frame = buffer.tobytes()
            yield (b'--frame\r\n'
                   b'Content-Type: image/jpeg\r\n\r\n' + frame + b'\r\n')

@app.route('/video_feed')
def video_feed():
    return Response(generate_frames(),mimetype='multipart/x-mixed-replace; boundary=frame')

if __name__ == '__main__':
    # Run the server using a threaded server to handle multiple clients more efficiently
 
    monkey.patch_all()
    http_server = WSGIServer(('192.168.4.1', 5000), app)
    http_server.serve_forever()

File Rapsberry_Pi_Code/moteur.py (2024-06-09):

import RPi.GPIO as GPIO


class Moteurs : 
	
	"""
	This comment shows how the motors pins are seperated in the code.
		  front
	+--+---------+--+	
	|\ |F1     F2| /|
	|\ |enA   enB| /|
	+--+		 +--+
	   |         |
	   |         |
	+--+		 +--+
	|/ |enB	  enA| \|
	|/ |B1	   B2| \|
	+--+---------+--+
		   back
	"""
	pinsBackMotors = {
		"enA" : -1,
		"enB" : -1,
		"in1" : -1,
		"in2" : -1,
		"in3" : -1,
		"in4" : -1
	}
	pinFrontMotors = {
		"enA" : -1,
		"enB" : -1,
		"in1" : -1,
		"in2" : -1,
		"in3" : -1,
		"in4" : -1
		
	}
	
	coordsTranslation = [0,0]
	coordsRotation = [0,0]
	pwmEnA = 0
	pwmEnB = 0
	
	MAXIMUM_PWM = 50
	
	# Constantes Translation
	MAX_XCOORDS_TRANS = 50
	MIN_XCOORDS_TRANS = -50
	
	MAX_YCOORDS_TRANS= 50
	MIN_YCOORDS_TRANS = -50
	
	# Constantes Rotation
	MAX_XCOORDS_ROT= 50
	MAX_YCOORDS_ROT = 50
	
	MIN_XCOORDS_ROT = -50
	MIN_YCOORDS_ROT = -50
	
	# Constantes Dead Point
	
	MAX_XCOORDS_DEAD = 20
	MIN_XCOORDS_DEAD = -20
	
	MAX_YCOORDS_DEAD= 20
	MIN_YCOORDS_DEAD = -20
	
	def __init__ (self, EnA, EnB, backIn1,backIn2,backIn3,backIn4,frontIn1,frontIn2,frontIn3,frontIn4) :
		self.pinBackMotors  = {
			"enA" : EnA,
			"enB" : EnB,
			"in1" : backIn1,
			"in2" : backIn2,
			"in3" : backIn3,
			"in4" : backIn4
		}
		
		self.pinFrontMotors  = {
			"enA" : EnA,
			"enB" : EnB,
			"in1" : frontIn1,
			"in2" : frontIn2,
			"in3" : frontIn3,
			"in4" : frontIn4
		} 
		GPIO.setmode(GPIO.BCM)
		
		
		GPIO.setup(EnA,GPIO.OUT)
		GPIO.setup(EnB,GPIO.OUT)
		
		self.pwmEnA = GPIO.PWM(EnA,100)
		self.pwmEnB = GPIO.PWM(EnB,100)
		self.pwmEnA.start(0)
		self.pwmEnB.start(0)

		# Moteurs Front
		
		GPIO.setup(frontIn1,GPIO.OUT)
		GPIO.setup(frontIn2,GPIO.OUT)
		GPIO.setup(frontIn3,GPIO.OUT)
		GPIO.setup(frontIn4,GPIO.OUT)
		
		
		# Moteurs Back
		GPIO.setup(backIn1,GPIO.OUT)
		GPIO.setup(backIn2,GPIO.OUT)
		GPIO.setup(backIn3,GPIO.OUT)
		GPIO.setup(backIn4,GPIO.OUT)


	def reset_PWM (self):
		GPIO.output(self.pinFrontMotors["in1"], GPIO.LOW)
		GPIO.output(self.pinFrontMotors["in2"], GPIO.LOW)
		GPIO.output(self.pinBackMotors["in1"], GPIO.LOW)
		GPIO.output(self.pinBackMotors["in2"], GPIO.LOW)
		GPIO.output(self.pinFrontMotors["in3"], GPIO.LOW)
		GPIO.output(self.pinFrontMotors["in4"], GPIO.LOW)
		GPIO.output(self.pinBackMotors["in3"], GPIO.LOW)
		GPIO.output(self.pinBackMotors["in4"], GPIO.LOW)
		self.pwmEnA.ChangeDutyCycle(0)
		self.pwmEnB.ChangeDutyCycle(0)
	
	# side is either "front" or "back"	
	# motor is the motor name (F1,F2,B1,B2)
	# isClockWise == true clock wise else its counter clockwise
	
	def moveMotor(self, side, motor, speed, isForward):
		if side == "front":
			if motor == "F1":
				if speed == 0:
					GPIO.output(self.pinFrontMotors["in1"], GPIO.LOW)
					GPIO.output(self.pinFrontMotors["in2"], GPIO.LOW)
				elif isForward == True:
					GPIO.output(self.pinFrontMotors["in1"], GPIO.LOW)
					GPIO.output(self.pinFrontMotors["in2"], GPIO.HIGH)
				else:
					GPIO.output(self.pinFrontMotors["in2"], GPIO.LOW)
					GPIO.output(self.pinFrontMotors["in1"], GPIO.HIGH)
				self.pwmEnA.ChangeDutyCycle(speed)
			elif motor == "F2":
				if speed == 0:
					GPIO.output(self.pinFrontMotors["in3"], GPIO.LOW)
					GPIO.output(self.pinFrontMotors["in4"], GPIO.LOW)
				elif isForward == True:
					GPIO.output(self.pinFrontMotors["in4"], GPIO.LOW)
					GPIO.output(self.pinFrontMotors["in3"], GPIO.HIGH)
				else:
					GPIO.output(self.pinFrontMotors["in3"], GPIO.LOW)
					GPIO.output(self.pinFrontMotors["in4"], GPIO.HIGH)
				self.pwmEnB.ChangeDutyCycle(speed)
			return
		elif side == "back":
			if motor == "B2":
				if speed == 0:
					GPIO.output(self.pinBackMotors["in1"], GPIO.LOW)
					GPIO.output(self.pinBackMotors["in2"], GPIO.LOW)
				elif isForward == True:
					GPIO.output(self.pinBackMotors["in1"], GPIO.LOW)
					GPIO.output(self.pinBackMotors["in2"], GPIO.HIGH)
				else:
					GPIO.output(self.pinBackMotors["in2"], GPIO.LOW)
					GPIO.output(self.pinBackMotors["in1"], GPIO.HIGH)
				self.pwmEnA.ChangeDutyCycle(speed)
			elif motor == "B1":
				if speed == 0:
					GPIO.output(self.pinBackMotors["in3"], GPIO.LOW)
					GPIO.output(self.pinBackMotors["in4"], GPIO.LOW)
				if isForward == True:
					GPIO.output(self.pinBackMotors["in3"], GPIO.LOW)
					GPIO.output(self.pinBackMotors["in4"], GPIO.HIGH)
				else:
					GPIO.output(self.pinBackMotors["in4"], GPIO.LOW)
					GPIO.output(self.pinBackMotors["in3"], GPIO.HIGH)
				self.pwmEnB.ChangeDutyCycle(speed)
			return
		else:
			print("error, no side found")
			
	# coordsRotation is a table of lenght 2
	def rotation(self, coordsRotation) :
		if coordsRotation[0] >= self.MAX_XCOORDS_ROT :
			coordsRotation[0] = self.MAX_XCOORDS_ROT
		elif coordsRotation[0] <= self.MIN_XCOORDS_ROT :
			coordsRotation[0] = self.MIN_XCOORDS_ROT
             
		if coordsRotation[0] < self.MAX_XCOORDS_DEAD and coordsRotation[0] > self.MIN_XCOORDS_DEAD :
			return
		# rotationClockWise 
		elif coordsRotation[0] > self.MAX_XCOORDS_ROT/2 :
			self.moveMotor("front", "F1", (abs(coordsRotation[0])/self.MAX_XCOORDS_ROT) * self.MAXIMUM_PWM , True)
			self.moveMotor("front", "F2", (abs(coordsRotation[0])/self.MAX_XCOORDS_ROT) * self.MAXIMUM_PWM , False)
			self.moveMotor("back", "B1", (abs(coordsRotation[0])/self.MAX_XCOORDS_ROT) * self.MAXIMUM_PWM , True)
			self.moveMotor("back", "B2", (abs(coordsRotation[0])/self.MAX_XCOORDS_ROT) * self.MAXIMUM_PWM , False)
		elif coordsRotation[0] < self.MAX_XCOORDS_ROT/2 :
			self.moveMotor("front", "F1", (abs(coordsRotation[0])/self.MAX_XCOORDS_ROT) * self.MAXIMUM_PWM , True)
			self.moveMotor("front", "F2", (abs(coordsRotation[0])/self.MAX_XCOORDS_ROT) * self.MAXIMUM_PWM , False)
			self.moveMotor("back", "B1", (abs(coordsRotation[0])/self.MAX_XCOORDS_ROT) * self.MAXIMUM_PWM , True)
			self.moveMotor("back", "B2", (abs(coordsRotation[0])/self.MAX_XCOORDS_ROT) * self.MAXIMUM_PWM , False)
	
	#  coordsTranslation is a table of length 2
	def translation(self, coordsTranslation) :
		if coordsTranslation[0] >= self.MAX_XCOORDS_TRANS :        
			coordsTranslation[0] = self.MAX_XCOORDS_TRANS
		elif coordsTranslation[0] <= self.MIN_XCOORDS_TRANS :
			coordsTranslation[0] = self.MIN_XCOORDS_TRANS
			
		if coordsTranslation[1] >= self.MAX_YCOORDS_TRANS :
			coordsTranslation[1] = self.MAX_YCOORDS_TRANS
		elif coordsTranslation[1] <= self.MIN_YCOORDS_TRANS :
			coordsTranslation[1] = self.MIN_YCOORDS_TRANS
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

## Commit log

2024-04-30 Adding servos + updating motors algorithm
2024-05-06 Adding Unity app
    [Schéma élec.fzz]
2024-05-07 Update raspberry pi
2024-05-13 Adding hardware support on the motors
    Please don't change the pins T_T
2024-06-06 Adding unity application
    [Schéma élec.fzz]
2024-06-07 Adding video streaming and fixing restore network and setup_network
    [moteur.py, video_stream.py]
2024-06-07 Organising files
    [Schéma élec.fzz]
2024-06-07 Updating README-RaspberryPi
2024-06-08 Adding README and schematics
    [Schéma élec.fzz]
2024-06-09 Ajout du rapport de conception
2024-06-09 Update Schéma élec
    [Schéma élec.fzz]
2024-06-19 Adding fusion files, datasheet and rapport
    [Assemblage bravabot.f3z, Base roulante.f3d, Canon.f3d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]
